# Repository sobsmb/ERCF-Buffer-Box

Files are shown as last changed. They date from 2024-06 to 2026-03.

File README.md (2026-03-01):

# ERCF-Buffer-Box

<p align="center">
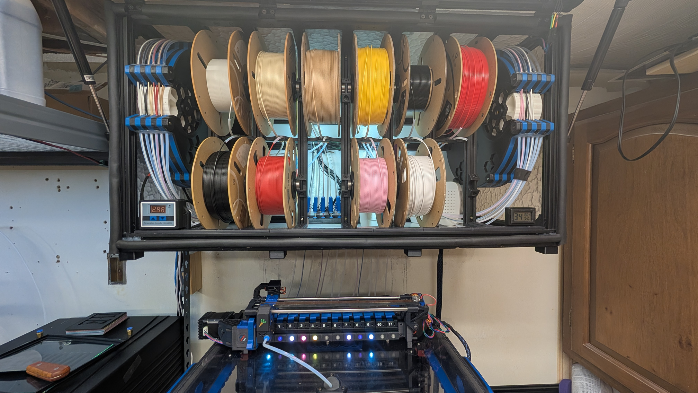
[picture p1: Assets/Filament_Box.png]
Buffer-Box
  
</p>

12 Spool Buffer Filament Box for the ERCF v2 (Updated March 2026)

## BOM

12 x [M4 Roll-in T-nuts](https://www.amazon.com/dp/B07VHNZ9XG)<br>
12 x [M4 x 10mm Flat Head](https://a.co/d/0fNCq3q4)<br>
~130 x [M5 Roll-in T-nuts](https://www.amazon.com/dp/B07VHNGBWJ)<br>
126 x [M5 x 10mm Flat Head](https://a.co/d/01dUSnKL)<br>
4 x [PC4-M10 Male Straight Pneumatic PTFE Tube Push-In Quick Fitting Connector](https://a.co/d/0e4PLHHR)<br>
2 x [10 Inch 100N/22.5lb Gas Struts](https://www.amazon.com/dp/B09BYY65W1)<br>
20ft x [Weather Stripping, D-shaped Rubber Seal Strip](https://www.amazon.com/dp/B0CCRXHYT7)<br>
~32 x [2020 Series L-Shape Interior Inside Corner Connector](https://www.amazon.com/dp/B08D6T9CGN)<br>
~12 x [2028 Corner Bracket](https://www.amazon.com/dp/B0BFRB35Z8)<br>
~15,000mm x [2020 V-slot Aluminum Extrusion](https://www.amazon.com/dp/B0BM8H5XZ9)<br>
~24 x [608-2RS Skateboard Bearing](https://www.amazon.com/gp/product/B073ST742Z)<br>
1 x [Under Cabinet Light, 12 Inch Plug-in LED Closet Light, 2pk](https://www.amazon.com/gp/product/B08VDH1GJV)<br>
LOTS x [PTFE Tube 3mm ID, 4mm OD](https://www.aliexpress.us/item/2251832878144608.html)<br>

## 2026 Updates

See `Spool Holder 2026 Edition` in the STL folder.

* No more [Stern-Wheeler](https://www.printables.com/model/472316-stern-wheeler). I had too much trouble getting these to work correctly. I kept getting false jams or actual jams because there was too much friction. I’m now using the [Integrated Auto-Rewind Spool Holder](https://www.thingiverse.com/thing:3781815) and made a custom profile that works very well. Models are included, but due to the size of the ones I included, they may not work for you. You may need to “play” with the Integrated Auto-Rewind Spool Holder’s diameter for your needs. The new spool holders also use less hardware. I've included my SCAD settings if you want to start there — see `/STL/Spool Holder 2026 Edition/IntegratedRewinderv5_6_1 Settings.txt`.

* Also, for the Integrated Auto-Rewind Spool Holder — I don't know if this is required, but I think a couple spring sections were sticking together at some points, preventing the spools from rewinding. So I added `Large Divider.stl` and `Small Divider.stl`. These are 0.2mm spacers that go between each spring section. I printed these in PLA since PLA and PETG do not stick together. I haven't had that problem since.  
  **NOTE:** Printing a 1-layer PLA object and peeling it off is surprisingly fun. I printed a bunch of them and tossed any “bad” ones. Use a [plastic razor blade](https://a.co/d/0enmqdN7) for better luck.

* The `Guide.stl` and `Axle.stl` get glued together so it is easier to align the rewinder when installing them. The axle also snaps into the `Spool Mount.stl` on both sides so you know when it is seated and secure. Just make sure your printer is fairly dialed in when printing these parts.

## 2025 Updates

### Heater Controller Mount:
2 x M5 x 10mm Flat Head  
2 x M5 Roll-in T-nuts  
Misc screws for mounting  

### Heater and Fan (Rear of Cabinet):
2 x M5 x 10mm Flat Head  
2 x M5 Roll-in T-nuts  
Misc screws for mounting  

### Filament Box Temp Sensor:
2 x M5 x 10mm Flat Head  
2 x M5 Roll-in T-nuts  

### PTFE Quick Connect:
24 x [Bowden Collets](https://a.co/d/7jrjyus)<br>
26 x [6x3 mm Neodymium Magnets](https://a.co/d/eJB51Ad)<br>
Misc screws for mounting<br>

### Heater
1 x [Digital LED Temperature Controller Module](https://a.co/d/0iozePl6)<br>
1 x [Air Heater, PTC Ceramic Heating DC12V 50W](https://a.co/d/0bwOyqDZ)<br>
1 x [DC 12V 60W Power Supply](https://a.co/d/0igF9PvV)<br>

## 3D Models

[Integrated Auto-Rewind Spool Holder](https://www.thingiverse.com/thing:3781815)<br>
[2020 Print-In-Place Vertical Hinge](https://www.printables.com/model/794070-2020-print-in-place-vertical-hinge)<br>
[Voron 2.4 Exhaust Cover](https://www.printables.com/model/633527-voron-24-exhaust-cover)<br>

## Notes

* Spool holder parts do not need any hardware except two 608-2RS skateboard bearings. I cleaned all the grease from my bearings so they spin freely.
* Print the spool holder parts in PETG. It gives them more grip on the spool, and the internal springs stay more flexible.
* When gluing the Guide and Axle: the axle should be flat on the ground and the guide sticking straight up. The parts are **not** a friction fit — use PETG Gloop or super glue.
* The filament should follow the arrows on the side of the rewinder see `/Assets/Rewinder Assembly 6.jpg`
* I moved the ERCF outside of the box — it was a pain to clean or deal with issues when it was inside the box.
* I created a PTFE Quick Connect so I can more easily pull the ERCF away from the filament box.
* For the PTFE Quick Connect: print the female piece and the cap, then glue them together (super glue works great). See image below.
* I added some TPU feet under the box so when I pull it off the wall, I can set it down without damaging anything on the bottom.

## Wiring

I will not provide wiring instructions because if you have built a Voron, you can probably figure this out on your own — plus your setup is going to be very different than mine.

## Misc

I included some misc parts that I created for my setup that you are welcome to use.<br><br>

If you use the [Voron 2.4 Canopy](https://www.printables.com/model/568090-voron-24-canopy) and have a [BTT PITFT50](https://a.co/d/5EXvKxF):  
See: `/Misc/Corner.stl` and `/Misc/PITFT50 Mount.stl`<br><br>

To make wiring easier, I used a [14-pin Micro-Fit 3.0mm connector](https://www.aliexpress.us/item/2251832548943535.html)<br>
See: `/Misc/Back Plate.stl` and `/Misc/Port.stl`  
(P.S. I have a Voron 2.4 350, so the Back Plate may not fit yours.)

## Spool Holder Parts

<p align="center">
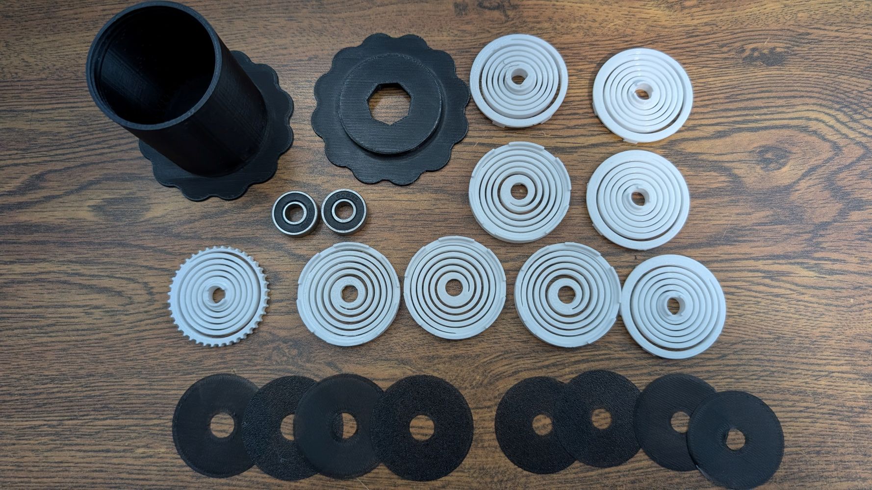
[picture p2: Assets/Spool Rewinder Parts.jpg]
Spool Rewinder parts
  <br>
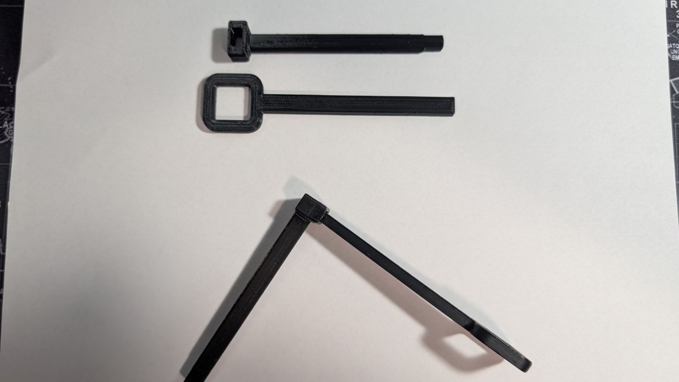
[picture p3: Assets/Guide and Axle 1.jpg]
Guide and Axle 1
  
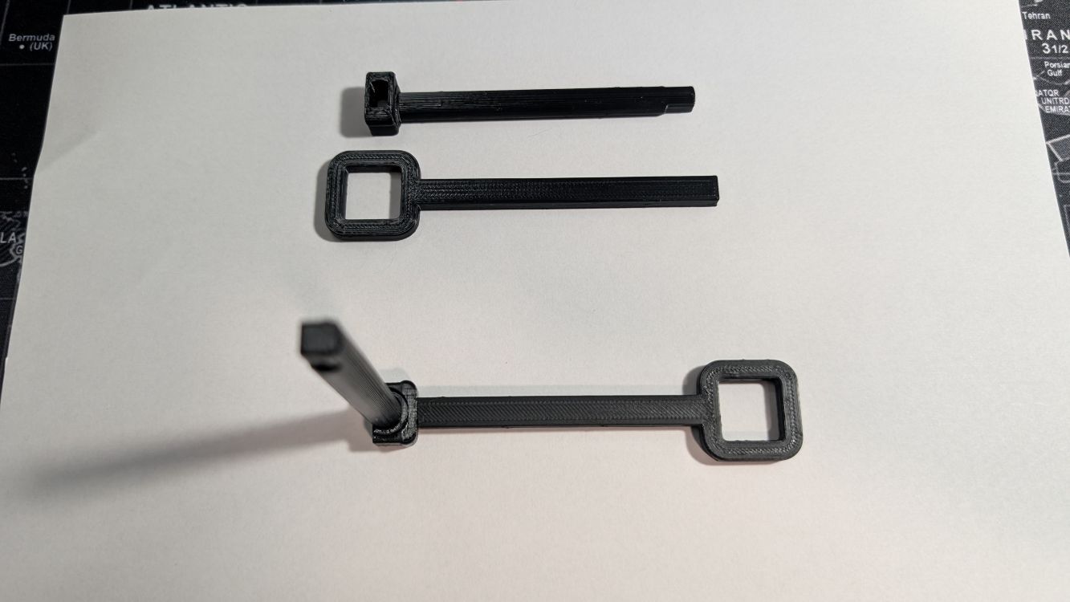
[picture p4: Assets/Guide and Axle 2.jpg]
Guide and Axle 2
  
</p>

## Spool Assembly

<p align="center">
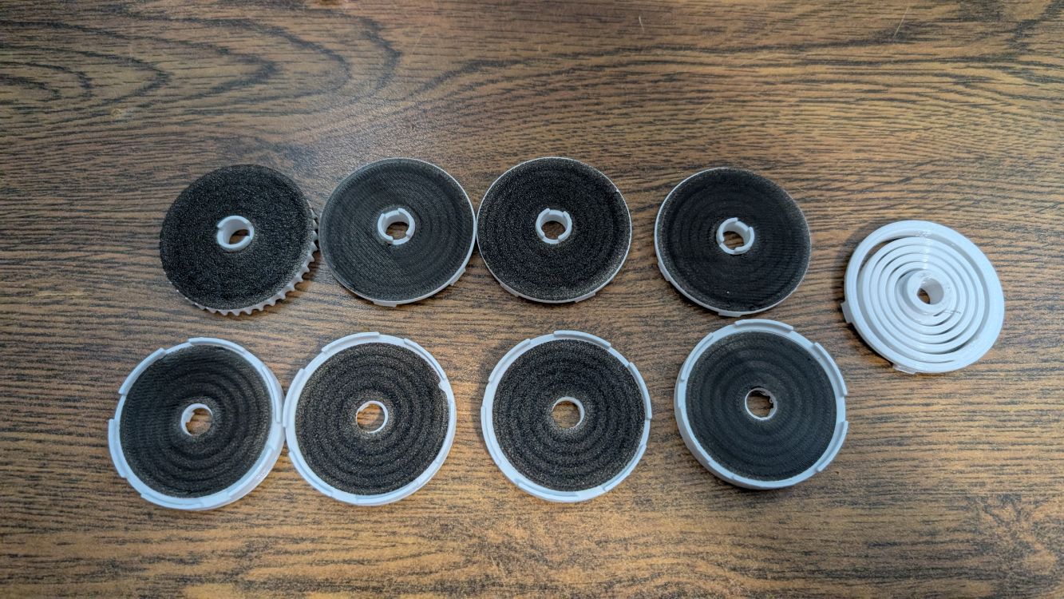
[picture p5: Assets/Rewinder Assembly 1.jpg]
Rewinder Assembly 1
  
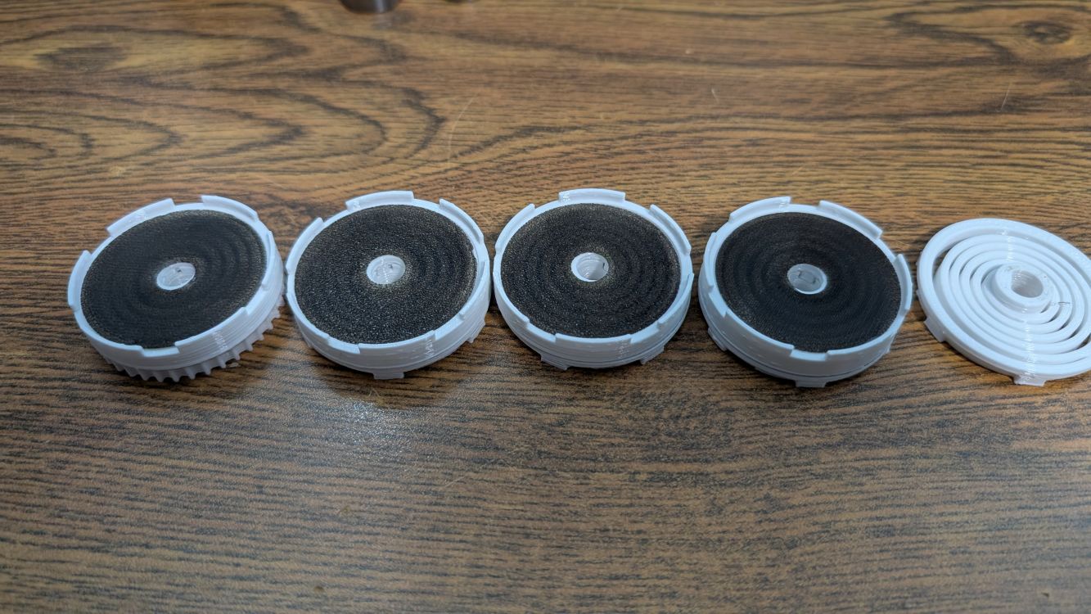
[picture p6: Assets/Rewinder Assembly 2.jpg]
Rewinder Assembly 2
  <br>
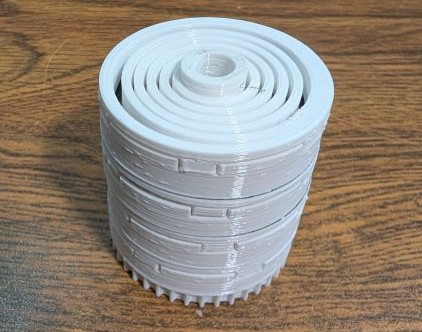
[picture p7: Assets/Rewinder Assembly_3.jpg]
Rewinder Assembly 3
  
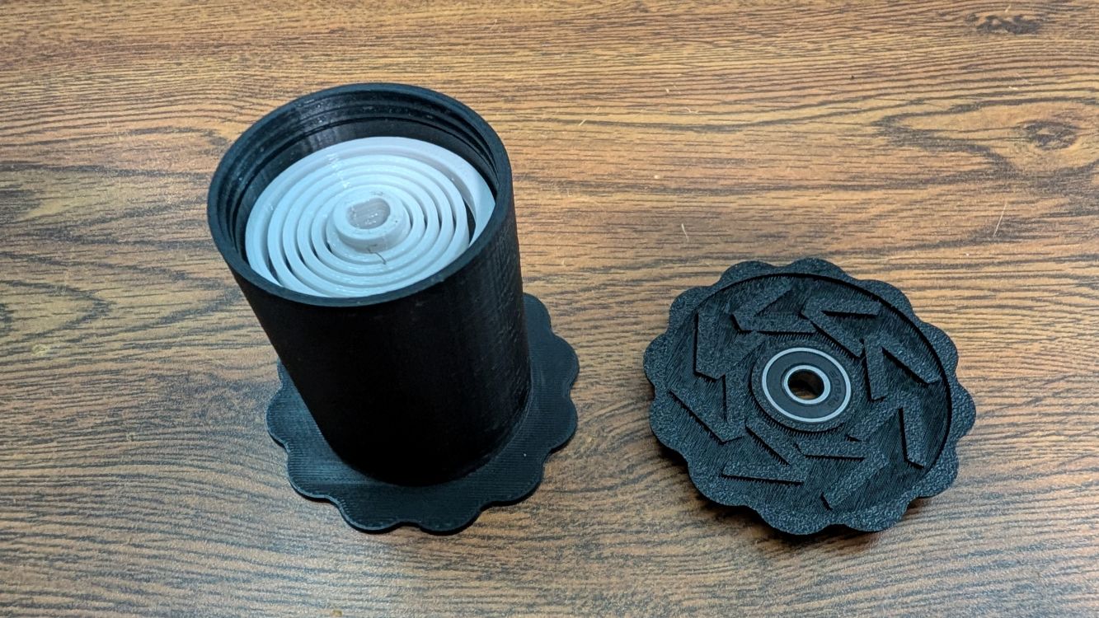
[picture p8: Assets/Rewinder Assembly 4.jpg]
Rewinder Assembly 4
  <br>
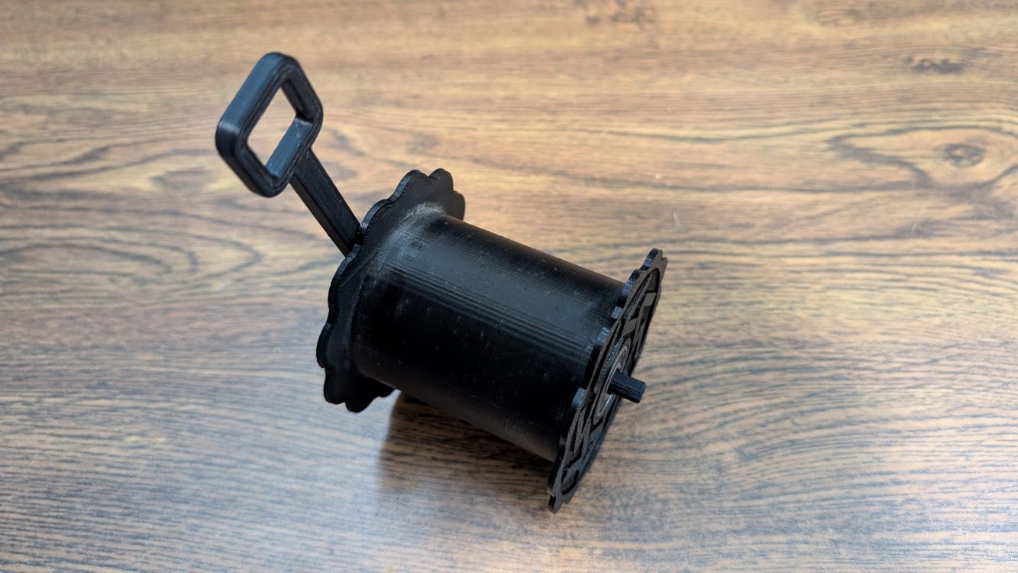
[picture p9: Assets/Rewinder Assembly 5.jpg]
Rewinder Assembly 5
  
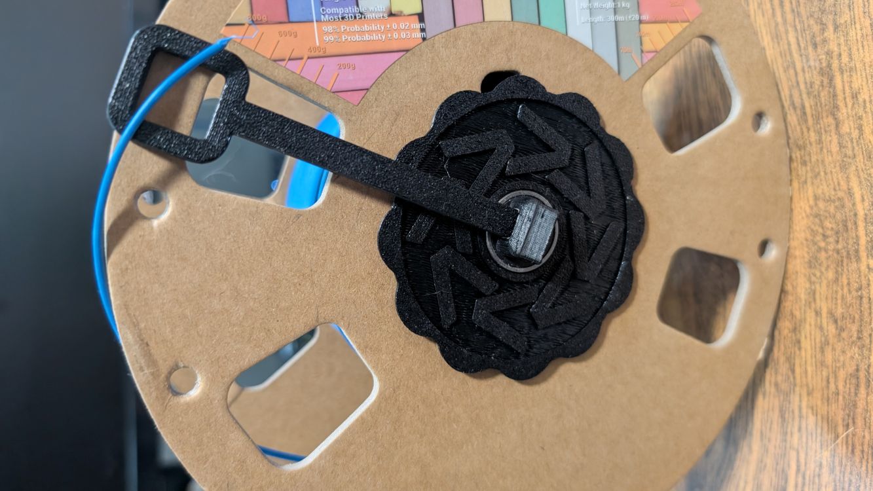
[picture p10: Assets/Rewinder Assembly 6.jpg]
Rewinder Assembly 6
  
</p>

## Misc Photos

<p align="center">
  Door Closed
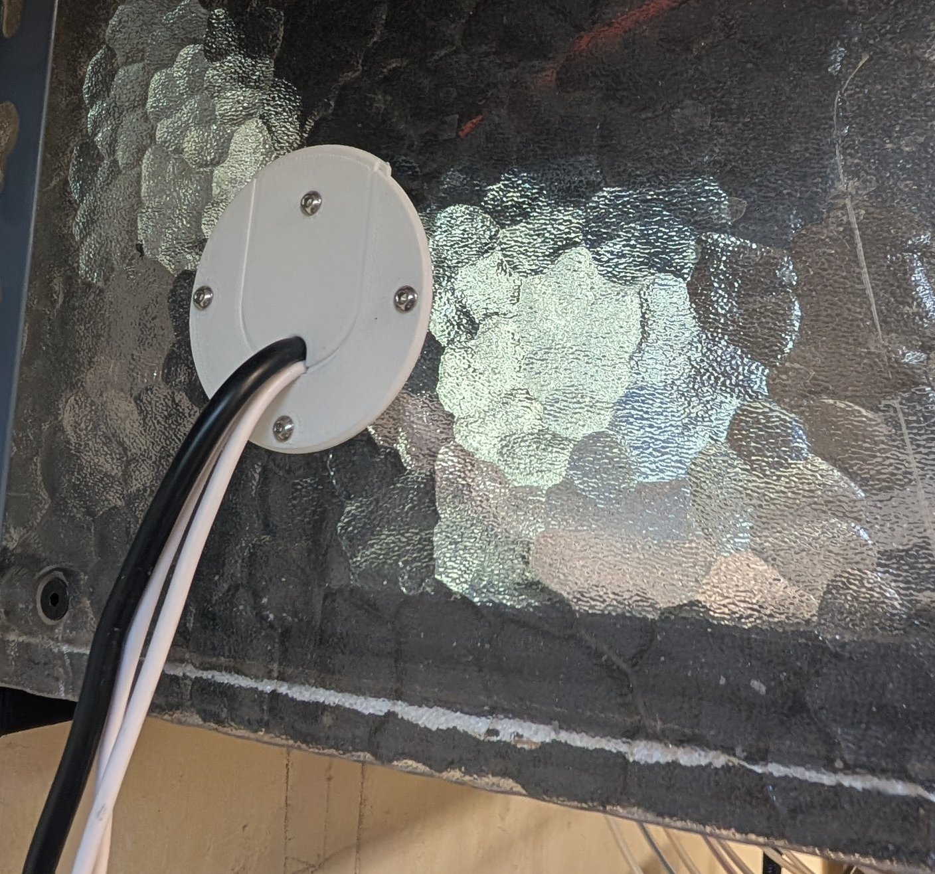
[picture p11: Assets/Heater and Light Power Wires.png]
Heater and Light Power Wires
  
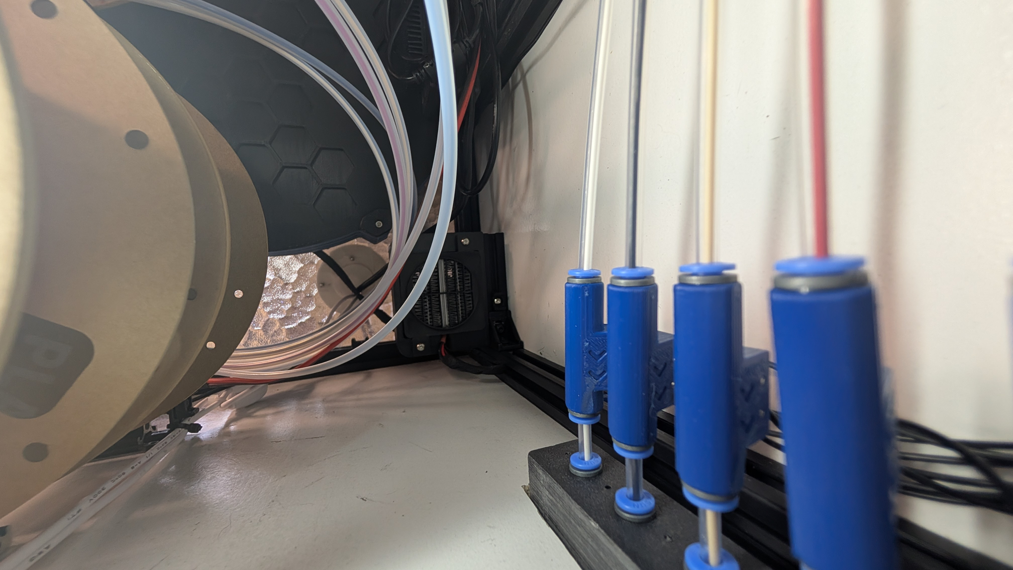
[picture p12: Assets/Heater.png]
Heater
  <br/>
  PITFT50 Mount
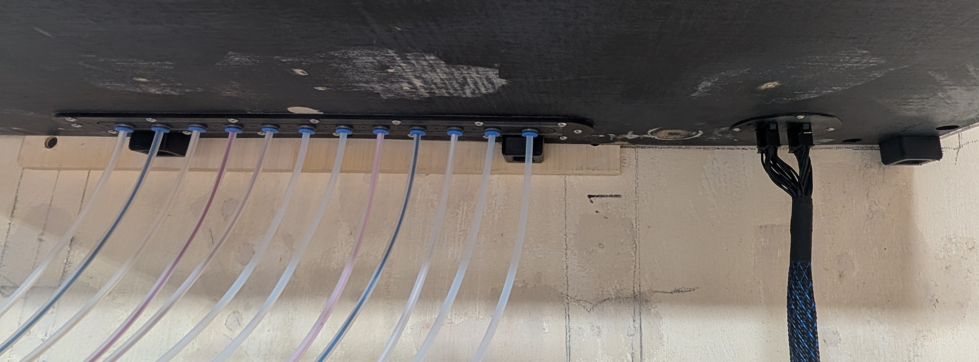
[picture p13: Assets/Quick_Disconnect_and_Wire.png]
Quick Disconnect and Wire
  
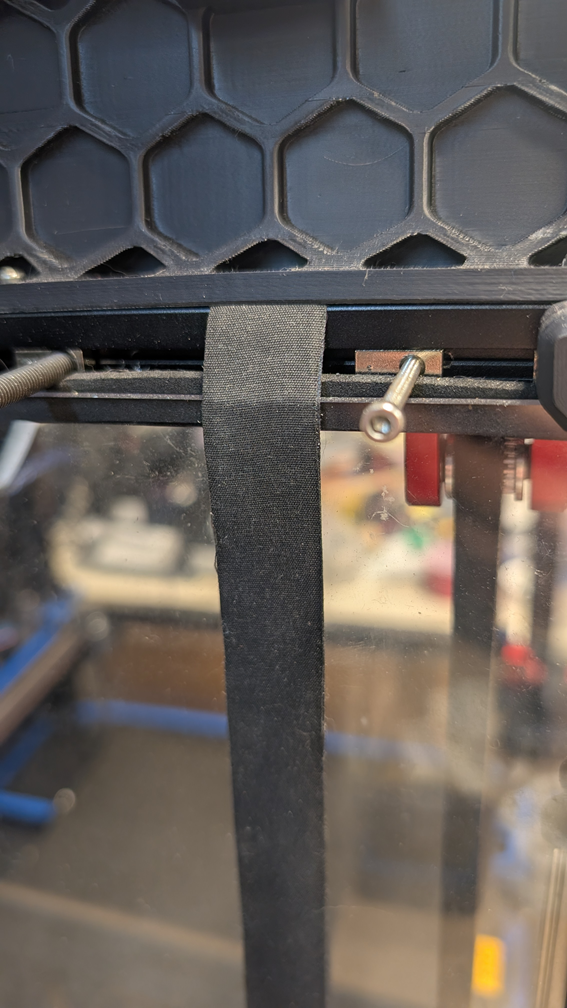
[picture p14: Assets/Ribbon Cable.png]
Ribbon Cable
  <br/>
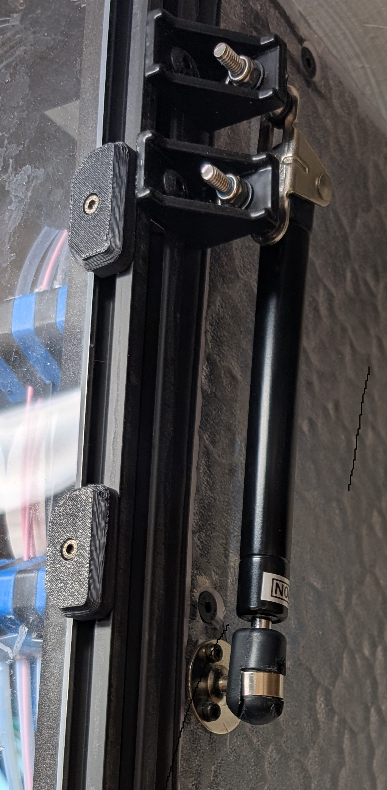
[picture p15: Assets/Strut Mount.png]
Strut Mount
  
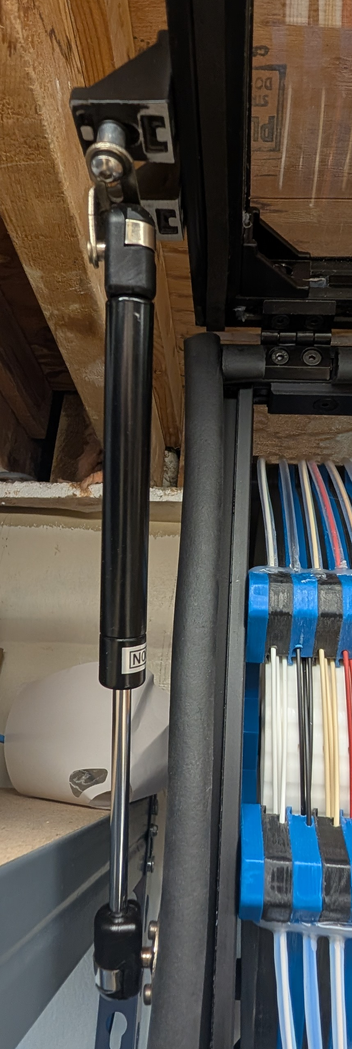
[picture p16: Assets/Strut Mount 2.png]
Strut Mount 2
  
</p>

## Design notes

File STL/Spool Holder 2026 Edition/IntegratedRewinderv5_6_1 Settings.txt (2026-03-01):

72 x 55 mm Spool Rewinder for IntegratedRewinder_v5_6_1.scad

output: print

universalRewinderSpring
rewinderLength: 69
springBladeCount: 9
rewinderDiameter: 55.0
rewinderSetRimDiameter: 80
axleDiameter: 8
hubRibDepth: 0
hubHoles: 0
embossDecals: true
embossCharacterTop: 
embossCharacterBottom: 
embossAlternateMirror: false
embossScale: 2
reverseSprings: false
springAlternate: true
springBladeThickness: 2.0
springBladePitch: 3
bearingDiameter: 22.2
bearingWidth: 7
halloween: 0

Advanced Parameters
$fn: 70
axleClearance: 0.3
axleConnectionDiameter: 13.5
bearingChamfer: 0.5
bearingCoverThickness: 1.4
hubHoleRelSize: 0.75
hubForceLevelCount: 4
hubHoleLevelSpacingFactor: 0.9
hubRibCount: 60
hubRibWidth: 0.7
hubHoleCount: 4
hubHolePolygonSize: 6
threadPitch: 0.75
threadDepth: 0.75
intertwinedThreadCount: 1
threadClearance: 0.4
rewinderRimThickness: 2.5
rewinderWallThickness: 2.5
springRimThickness: 2.5
springHubClearance: 1
springThresholdSpace: 0.5
springFlatShaft: true
springFlatShaftLength: 3
springRoundShaftLength: 6
springBaseTabCount: 40
springOuterTabCount: 6
springInnerTabCount: 6
springTabThickness: 1.3
springRadialTabClearance: 0.05
springBaseRadialTabClearance: 0.05
springCircularTabClearance: 0.5
springVerticalTabClearance: 0.5
springBaseTabSizeFactor: 0.7
springTabSizeFactor: 0.7
springTabGapCurvedPartRemovalDepth: 0.4
springStackGap: 0.5
springTabHeightRel: 12
rimGripCount: 12
embossDepth: 1
embossEdgeThickness: 1
embossDecalCount: 4
universalBackplateThickness: 0.8

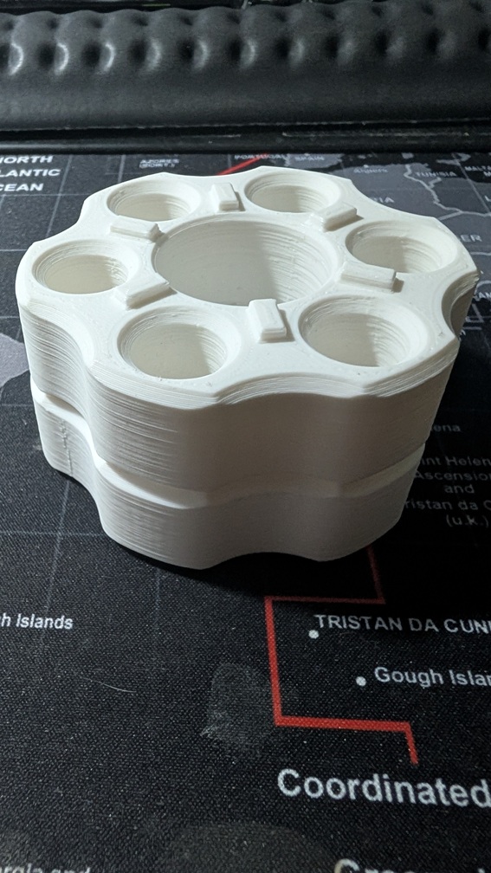
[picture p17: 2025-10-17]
Assets/Tools Stacked.jpg

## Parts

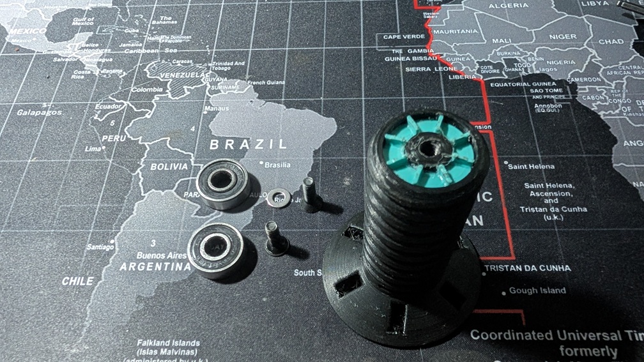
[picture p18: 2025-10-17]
Assets/Spool Holder parts.jpg

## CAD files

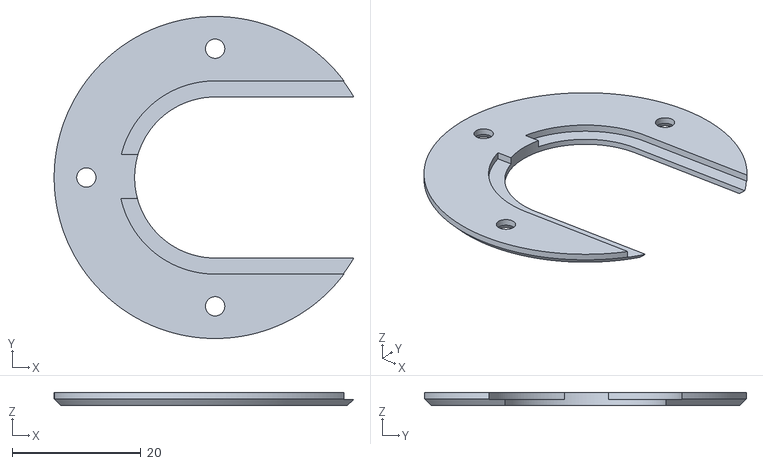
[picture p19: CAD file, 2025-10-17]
STL/25mm Wire Cover/Outer Body.stl
46.5 x 50.0 x 2.00

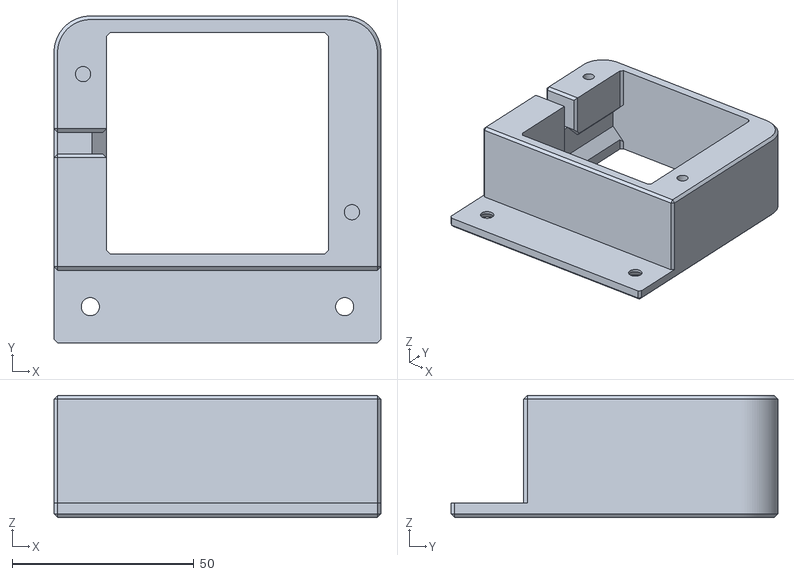
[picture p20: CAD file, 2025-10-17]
STL/50watt Heater/Heater.stl
90.0 x 90.0 x 33.6

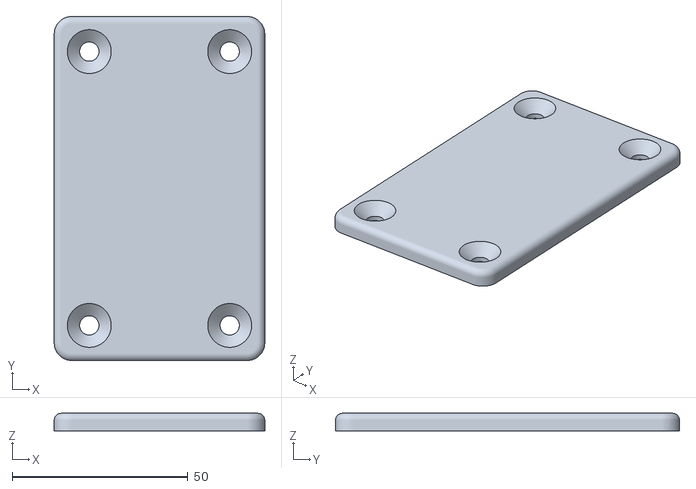
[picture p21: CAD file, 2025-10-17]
STL/ERCF Spacer.stl
60.0 x 98.0 x 5.00

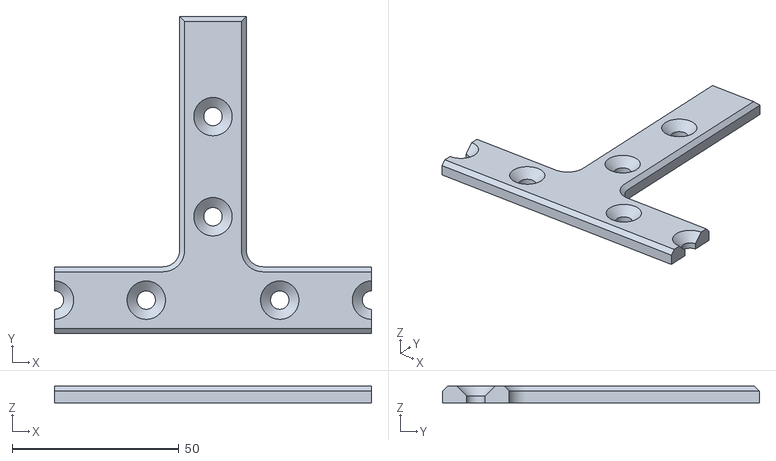
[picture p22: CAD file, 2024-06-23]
STL/Hanger Mounts/Normal T.stl
95.0 x 95.0 x 5.00

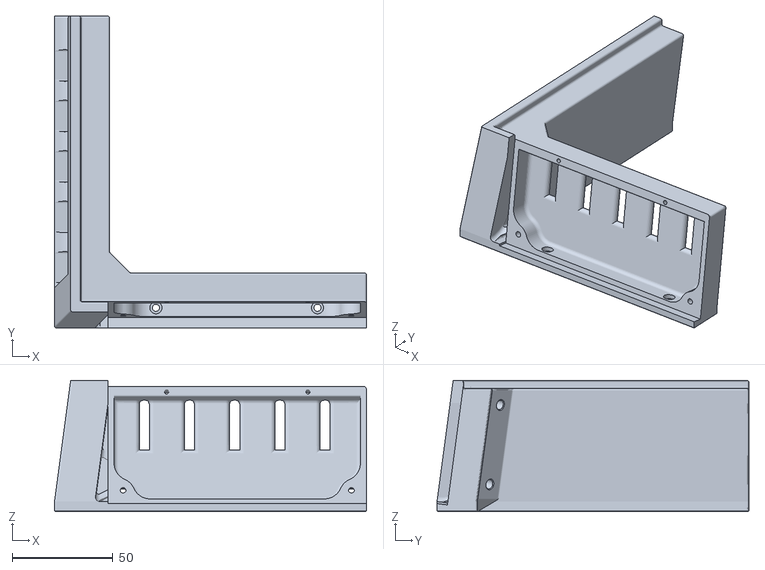
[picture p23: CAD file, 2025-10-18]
STL/Misc/Corner.stl
154.5 x 154.5 x 65.0

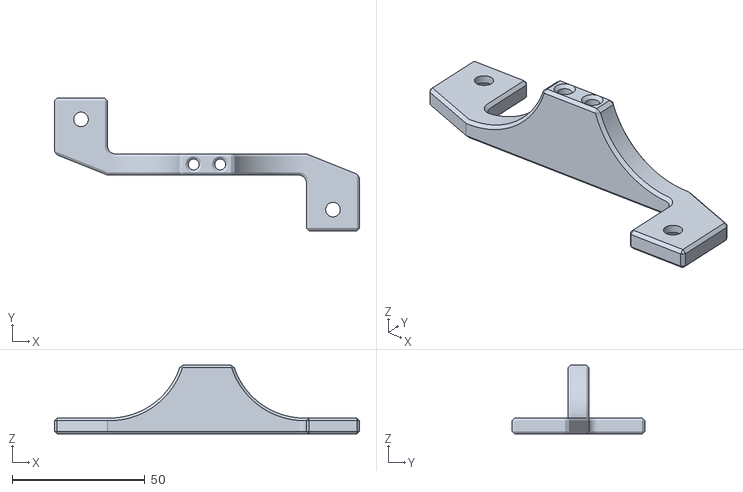
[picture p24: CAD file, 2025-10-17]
STL/PTFE Guides/Filament Path.stl
115.0 x 50.0 x 26.0

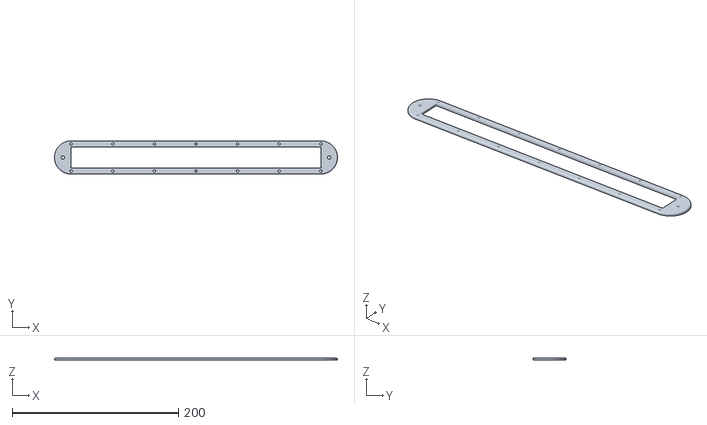
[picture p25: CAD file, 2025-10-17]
STL/PTFE Quick Connect/Cap.stl
340.0 x 40.0 x 3.00

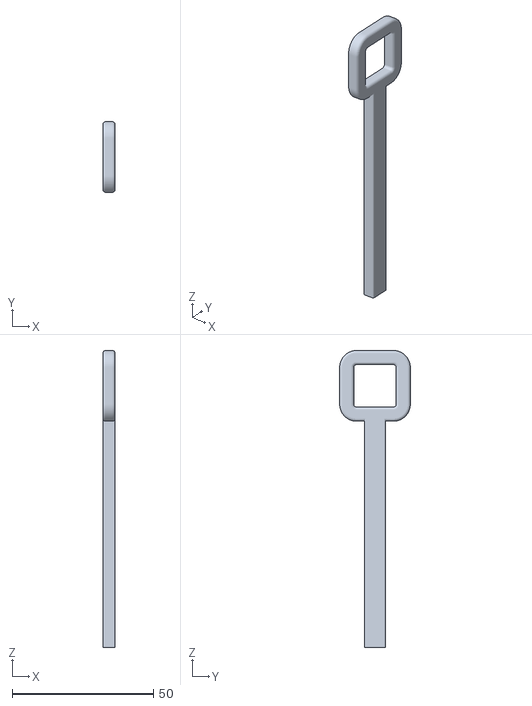
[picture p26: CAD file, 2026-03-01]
STL/Spool Holder 2026 Edition/Guide.stl
4.40 x 25.0 x 105.0

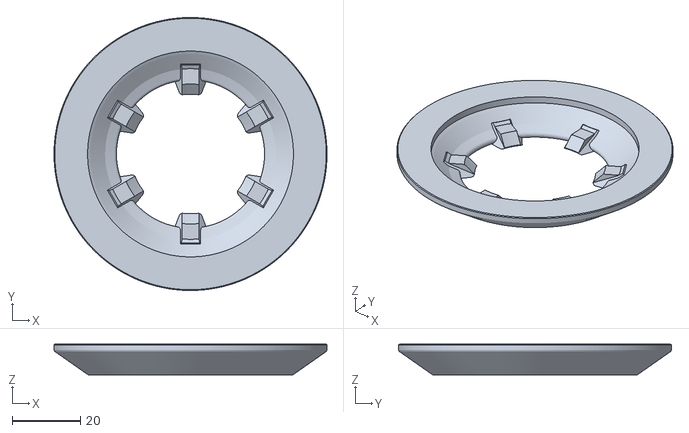
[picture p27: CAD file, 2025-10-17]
STL/Spool Holder/80mm Adapter.stl
80.0 x 80.0 x 9.00

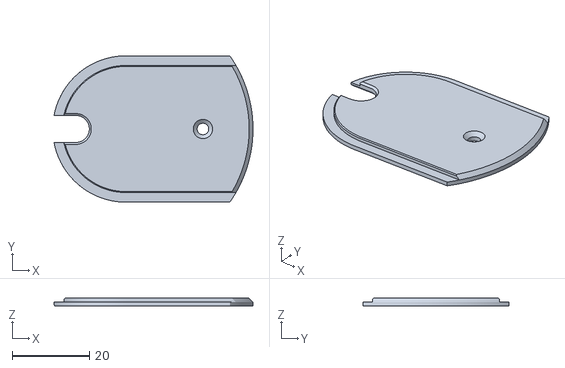
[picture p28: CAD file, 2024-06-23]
STL/25mm Wire Cover/Wire Passthrough.stl
51.7 x 38.0 x 2.00

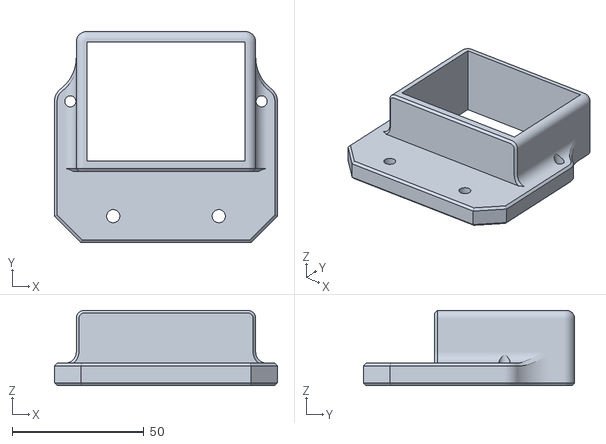
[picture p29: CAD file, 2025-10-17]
STL/50watt Heater/Controler Mount.stl
84.5 x 80.0 x 28.5

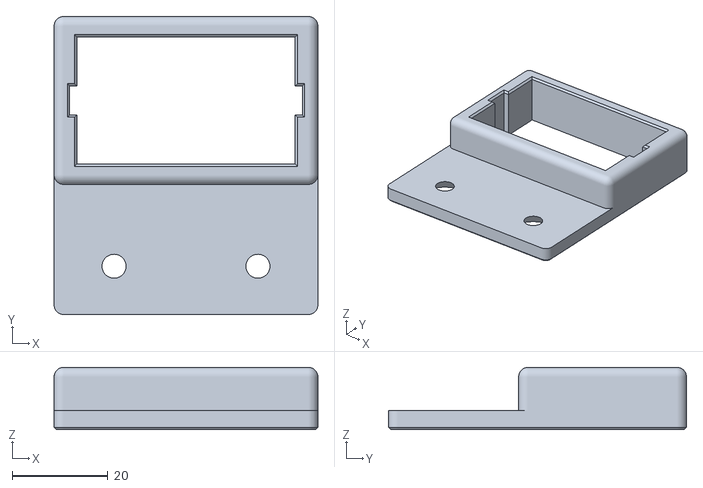
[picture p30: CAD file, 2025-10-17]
STL/Filament Box Temp Sensor.stl
55.0 x 62.1 x 13.0

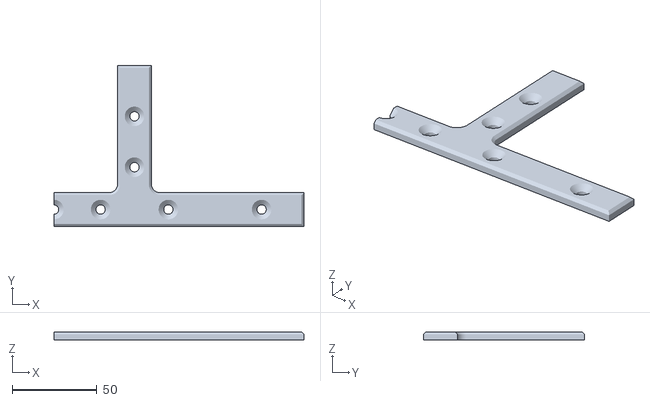
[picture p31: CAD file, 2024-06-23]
STL/Hanger Mounts/Right T.stl
147.5 x 95.0 x 5.00

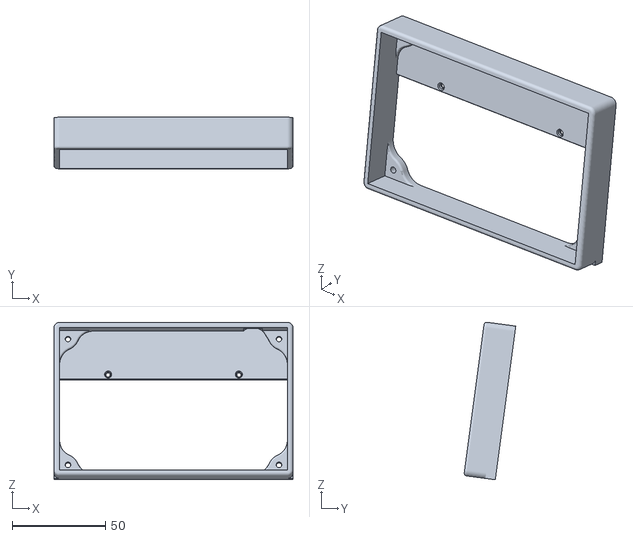
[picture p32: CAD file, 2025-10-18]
STL/Misc/PITFT50 Mount.stl
128.0 x 27.6 x 84.3

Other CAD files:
STL/PTFE Guides/Right Filament Path.stl
STL/PTFE Quick Connect/Male.stl
STL/Spool Holder 2026 Edition/Small Divider.stl
STL/Bearing Holder.stl
STL/Hanger Mounts/Left T.stl
STL/LED Mount.stl
STL/Misc/Back Plate.stl
STL/Misc/Port.stl
STL/OLD Spool Holder 2025 Edition/60mm Nut.stl
STL/OLD Spool Holder 2025 Edition/60mm Roller.stl
STL/OLD Spool Holder 2025 Edition/70mm Adapter.stl
STL/OLD Spool Holder 2025 Edition/Bearing Holder.stl
STL/OLD Spool Holder 2025 Edition/TPU Washer.stl
STL/OLD Spool Holder 2025 Edition/Tool.stl
STL/PTFE Guides/Left Filament Path.stl
STL/PTFE Quick Connect/Female.stl
STL/Spool Holder 2026 Edition/72 x 55 Spool Holder Parts.stl
STL/Spool Holder 2026 Edition/Axle.stl
STL/Spool Holder 2026 Edition/Large Divider.stl
STL/Spool Holder 2026 Edition/Spool Mount.stl
STL/Spool Holder/60mm Nut.stl
STL/Spool Holder/70mm Adapter.stl
STL/Spool Holder/TPU Washer.stl
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

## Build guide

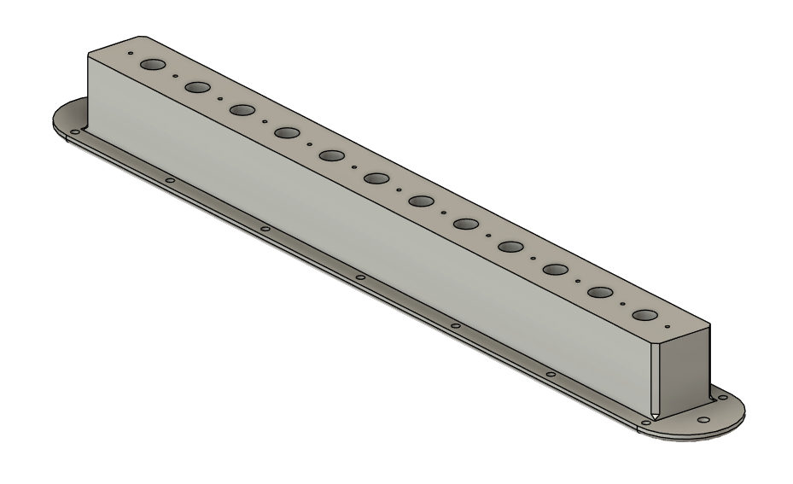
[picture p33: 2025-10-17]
Assets/Quick Connect Assembly.png

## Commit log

2024-06-23 Files/data added
    [60mm Nut.stl, 80mm Nut.stl, Bearing Holder.stl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]
2024-06-26 Spool Updates
    [60mm Nut.stl, 80mm Nut.stl, TPU Washer.stl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]
2025-10-18 More updates
    [60mm Washer TPU.stl, Back Plate.stl, Corner.stl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]
2026-03-01 2026 Updates
    [60mm Nut.stl, 60mm Roller.stl, 70mm Adapter.stl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]
2026-03-01 Update Rewinder Assembly 3.jpg
